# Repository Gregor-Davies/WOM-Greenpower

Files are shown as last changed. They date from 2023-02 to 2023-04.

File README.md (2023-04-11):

# Greenpower Winter Of Making

A telemetry system for a Greenpower racing go-kart (https://www.greenpower.co.uk/), built using LoRA and programmed with C++. This project has kindly been funded through the hack club winter of making grant program.

# Currently Implemented

- Temperature of the motor
- Speed of the vehicle
- Temperature of the batteries

TODO:

- Current sensor
- Braking notfications?
- Web app?
- SD Datalogging
- Bigger screens
- Graphing of results?
- Elapsed time of race
- Tyre pressure
- Strain sensor
- Better casing designs
- Gyroscope?
- Swith to imu?
- Battery voltage
- Test the range of the system
- Throttle position
- Battery Voltage
- Recording amp hours used
- Distance travelled
- Lap number

# System Diagram

Lora Diagram (1)

# Required Parts

| Product | Supplier/Link | Cost |
| --- | --- | --- |
| Heltec Lora32 v2  | https://bit.ly/3zlZaot Amazon  | $55  |
| DS18B20 Sensor| https://bit.ly/3VdB5J5  Amazon | $16 |
| 10000mah PowerBank | https://bit.ly/3v5uVju Amazon | $13 |
| 15k Ohm Resistors | https://bit.ly/3FLcQMF Amazon | $3 |
| 1k Potentiometer | https://bit.ly/3FJpsDI Amazon | $4 |
| 100nF Capacitors| https://bit.ly/3G6lmXE Amazon| $7 |
| Zener Diode | https://bit.ly/3HV55q9 Amazon | $2.5 |
| Perfboard | https://bit.ly/3G37gq5 Amazon | $6.5 |
| Right angle USB MICRO Cable | Already Have | $8 |
| Speed sensor | https://bit.ly/3WocDWD Amazon | $7 |
| 6.2k Resistors | https://bit.ly/3YDCV92 Amazon | $4.5 |
| Total | | $126.5 |

# Error Codes

- 1 LED BLINK: Oled initalization has failed, check if OLED pins are correct (By default they are) and if the OLED is visibly damaged.
- 2 LED BLINKS: No packet was recieved by the reciever, check antennas on both reciever and transmitter. 
- 3 LED BLINKS: Motor temperature is 85 C, this is normally an indicator that the DS18B20 sensors are broken or not working (Or your vehicle is running too hot).
- 4 LED BLINKS: Heatsink temperature is 85 C, this is normally an indicator that the DS18B20 sensors are broken or not working (Or your vehicle is running too hot).

## License

This project, code and all of it's respecting files is licensed under the AGPL v3 Copyleft license. This means that all projects utilising this code must also be opensource, please respect this.

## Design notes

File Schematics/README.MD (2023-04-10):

All the schematics for the project.

Battery schematic taken from https://forum.arduino.cc/t/the-cheapest-and-safest-method-to-read-car-battery-voltage/684897
Multiple ds18b20 sensors from https://randomnerdtutorials.com/esp32-multiple-ds18b20-temperature-sensors/

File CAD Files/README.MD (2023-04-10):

All the cad files for the project

Personally I printed the base station case on a ender 3 with the base standard quality Cura settings and at a 10% infill.

You will need to print 1 of everything apart for the battery holder where you will have to print 2.

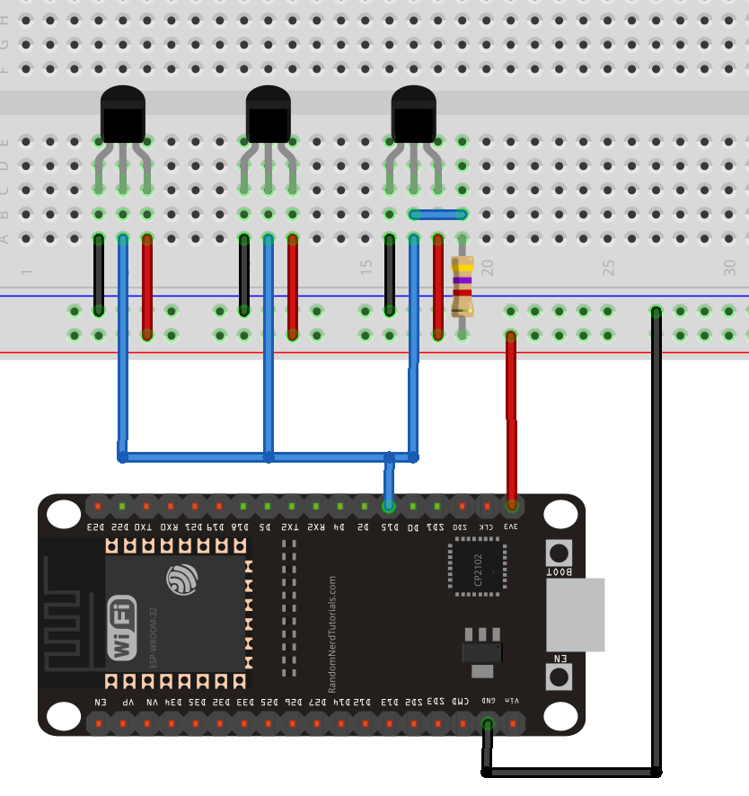
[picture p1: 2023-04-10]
Schematics/multiple_ds18b20_esp32_bb.png

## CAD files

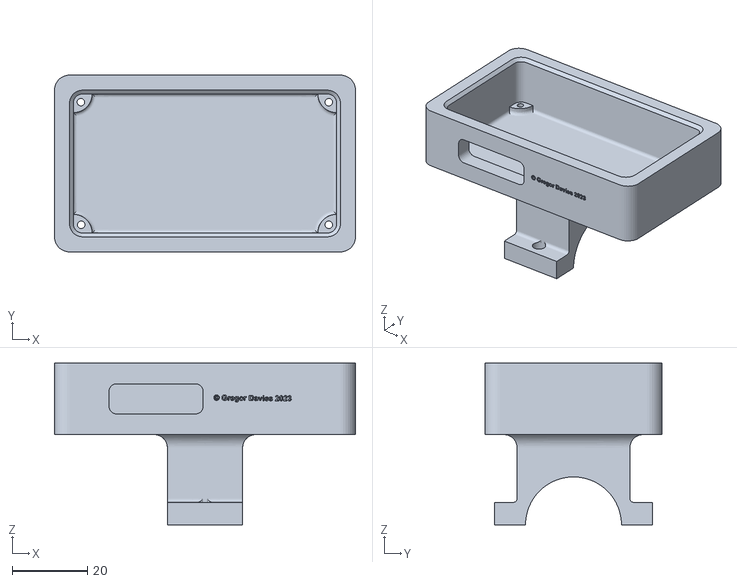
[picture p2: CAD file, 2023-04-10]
CAD Files/Greenpower temp case v7 Main.stl
80.0 x 47.0 x 43.0

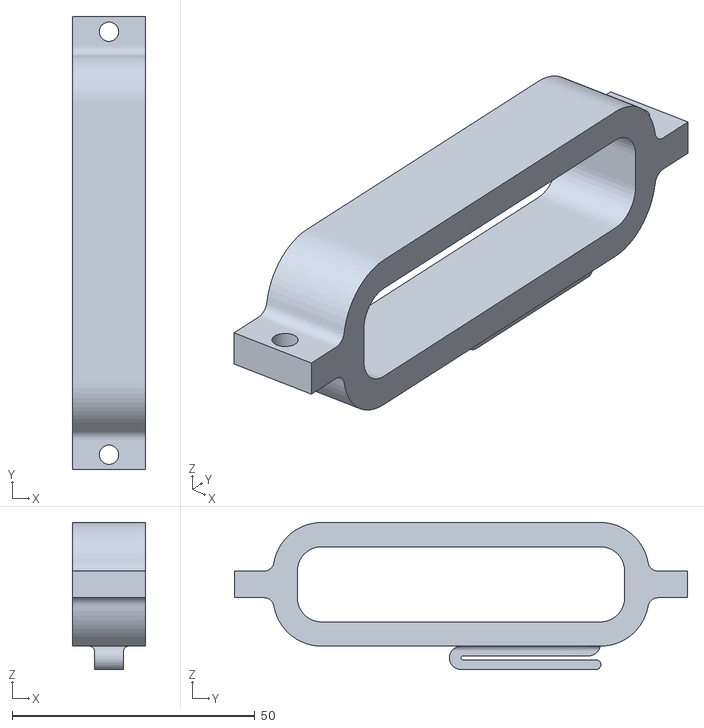
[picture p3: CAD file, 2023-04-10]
CAD Files/Battery Holder v1.stl
15.0 x 93.4 x 30.3

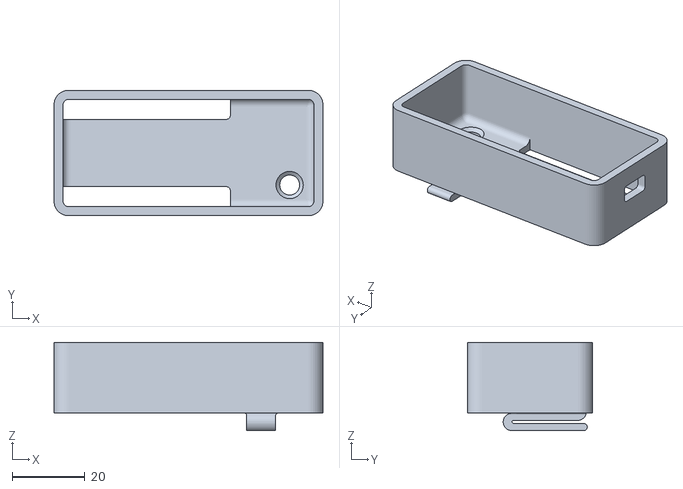
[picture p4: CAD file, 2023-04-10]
CAD Files/New heltec lora32 v2 case.stl
74.0 x 34.5 x 24.3

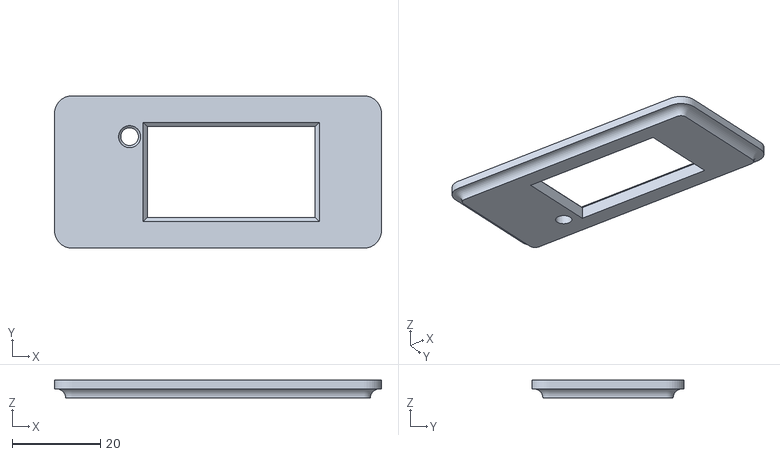
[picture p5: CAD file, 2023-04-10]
CAD Files/heltec lora32 v2 lid.stl
74.0 x 34.5 x 4.00

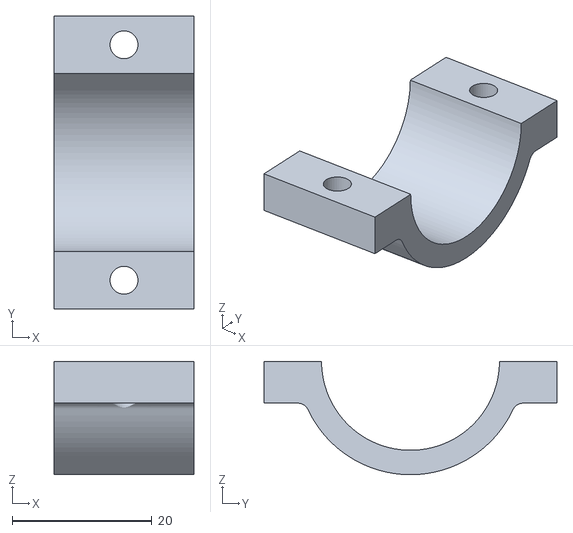
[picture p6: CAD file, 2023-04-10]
CAD Files/Greenpower temp case v7 loop.stl
20.0 x 42.0 x 16.2

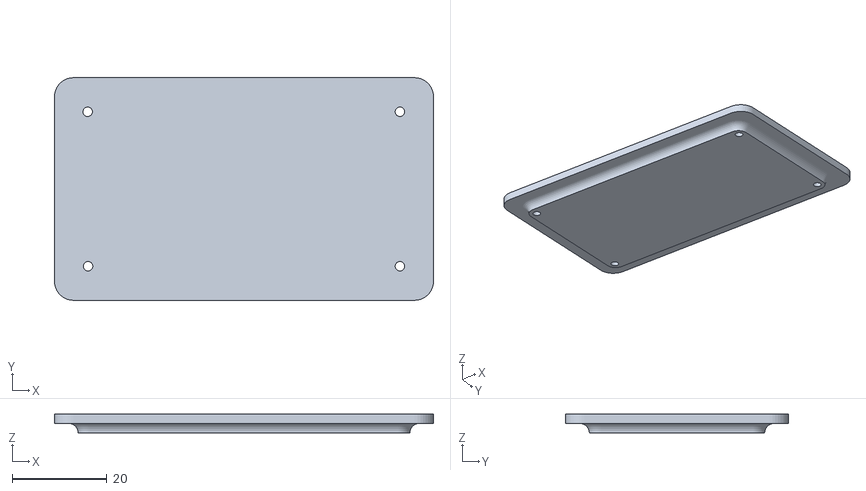
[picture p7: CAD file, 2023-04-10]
CAD Files/Greenpower temp case v7 lid.stl
80.0 x 47.0 x 4.00

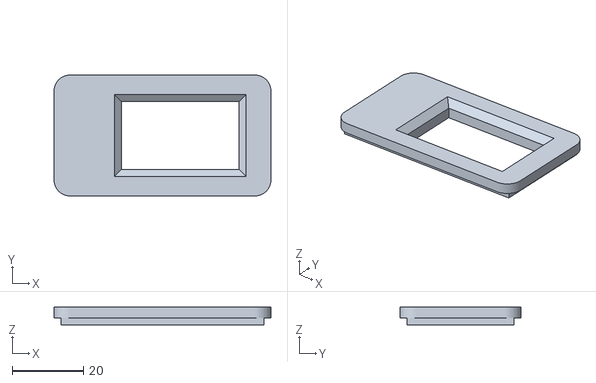
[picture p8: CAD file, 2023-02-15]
CAD Files/Case v2 Top.stl
61.0 x 34.0 x 5.00

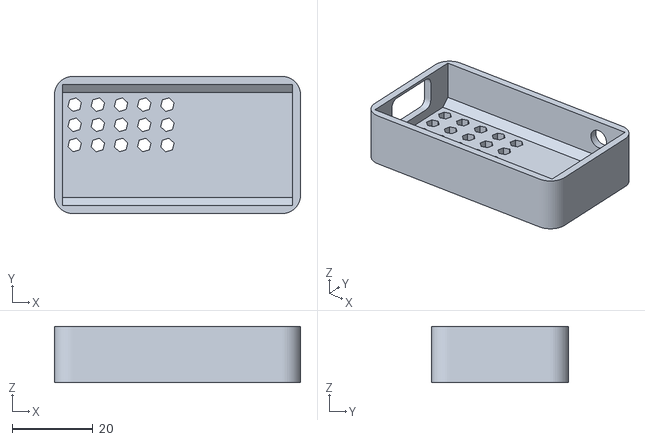
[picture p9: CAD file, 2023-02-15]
CAD Files/Case-Base v2.stl
61.0 x 34.0 x 14.0

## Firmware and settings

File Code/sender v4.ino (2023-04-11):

#include <LoRa.h>

// display stuff
#include <Wire.h>
#include <Adafruit_GFX.h>
#include <Adafruit_SSD1306.h>

// this stuff is for the temp sensor
#include <OneWire.h>
#include <DallasTemperature.h>

// defining the lora pins
#define ss 18
#define rst 14
#define dio0 26

// setting up the onewirebus on pin 23
const int oneWireBus = 23;

// setting up a one wire instance
OneWire oneWire(oneWireBus);

//pass one wire under the dallas temp lib
DallasTemperature sensors(&oneWire);

// Addressing the 2 temp sensors
DeviceAddress temp1 = {0x28, 0x35, 0xF7, 0x2E, 0xA1, 0x21, 0x1, 0x8C };
DeviceAddress temp2 = {0x28, 0xC9, 0x3, 0x33, 0xA1, 0x21, 0x1, 0x9f };

// defining the oled used
#define OLED_SDA 4
#define OLED_SCL 15 
#define OLED_RST 16
#define SCREEN_WIDTH 128 // OLED display width, in pixels
#define SCREEN_HEIGHT 64 // OLED display height, in pixels

// speed sensor is on pin check out the heltec lora32 v2 pin out diagram
const int LM393 = 17;
int counter = 0;

// starting the oled
Adafruit_SSD1306 display(SCREEN_WIDTH, SCREEN_HEIGHT, &Wire, OLED_RST);

void setup() {
  attachInterrupt(digitalPinToInterrupt(LM393), count, RISING);
  Serial.begin(115200);
  //reset OLED display via software
  pinMode(OLED_RST, OUTPUT);
  digitalWrite(OLED_RST, LOW);
  delay(20);
  digitalWrite(OLED_RST, HIGH);
  //initialize OLED
  Wire.begin(OLED_SDA, OLED_SCL);
  if(!display.begin(SSD1306_SWITCHCAPVCC, 0x3c, false, false)) { // Address 0x3C for 128x32
    Serial.println(F("SSD1306 allocation failed"));
    digitalWrite(LED_BUILTIN, HIGH); // error code 1: see github
    digitalWrite(LED_BUILTIN, LOW);    
    for(;;); // Don't proceed, loop forever
  }
  // setting the lora pins
  LoRa.setPins(ss, rst, dio0);
  LoRa.begin(866E6);
  LoRa.setSyncWord(0xF3);
  sensors.begin();
}

void count() {
  counter++;
}

// gets the sensors
void Sensors() {
  // Allowing the sensors time to do their stuff
  delay(500);
  char nonFloTemp[4];
  char nonFloBatteryTemp[4];
  char speedBuffer[15];
  char mTemp[25];
  char bTemp[25];
  char packetToSend[55];
  display.clearDisplay();
  // setting the colour to white and font size - this should always be white no matter what oled colour
  display.setTextColor(WHITE);
  display.setTextSize(1);
  // this converts the number to rpm and into kmh, the 60 is for rpm and the first number is wheel diameter in cm k = d * r * 0.001885
  int speed = 2.57 * counter * 60 * 0.001885;
  // getting the temp from the temperature sensors
  sensors.requestTemperatures();
  // getting the temp sensor at index 0 and converts the float to a string for sprintf
  float mTemperature = sensors.getTempC(temp1);
  dtostrf(mTemperature, 2, 0, nonFloTemp);
  if(mTemperature = 85) {
    digitalWrite(LED_BUILTIN, HIGH); // error code 3: see github
    digitalWrite(LED_BUILTIN, LOW);    
    digitalWrite(LED_BUILTIN, HIGH); //and yes I am doing like this as otherwise I would have to store an additional counter variable which is more memory intensive than just spaghetti code like this.
    digitalWrite(LED_BUILTIN, LOW);
    digitalWrite(LED_BUILTIN, HIGH); 
    digitalWrite(LED_BUILTIN, LOW);
  }
   // same thing but at index 1
  float bTemperature = sensors.getTempC(temp2);
  dtostrf(bTemperature, 2, 0, nonFloBatteryTemp);
  if(bTemperature = 85) {
    digitalWrite(LED_BUILTIN, HIGH); // error code 4: see github
    digitalWrite(LED_BUILTIN, LOW);    
    digitalWrite(LED_BUILTIN, HIGH); 
    digitalWrite(LED_BUILTIN, LOW);
    digitalWrite(LED_BUILTIN, HIGH); 
    digitalWrite(LED_BUILTIN, LOW);
    digitalWrite(LED_BUILTIN, HIGH); 
    digitalWrite(LED_BUILTIN, LOW);
  }
  // combines the speed and motor
  sprintf(speedBuffer, "SPEED: %d km/h", speed);
  sprintf(mTemp, "MOTOR TEMP: %sC", nonFloTemp);
  sprintf(bTemp, "BATTERY TEMP: %sC", nonFloBatteryTemp);
  // prints the speed, then sets the cursor one down and prints the temperature
  // sets cursor at 0
  display.setCursor(0,0);
  display.print(speedBuffer);
  display.setCursor(0,10);  
  display.print(mTemp);
  display.setCursor(0,20);
  display.print(bTemp);
  // Combining the things to send as one packet
  snprintf(packetToSend, 55, "%s,%s,%s", speedBuffer, mTemp, bTemp);
  // begins the lora packet
  LoRa.beginPacket();
  LoRa.print(packetToSend);
  LoRa.endPacket();
  counter = 0;
}

void loop() {
  Sensors();
  display.display();
}

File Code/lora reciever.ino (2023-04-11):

// lora libraries
#include <LoRa.h>

// lora pins
#define ss 18
#define rst 14
#define dio0 26

// display stuff
#include <Wire.h>
#include <Adafruit_GFX.h>
#include <Adafruit_SSD1306.h>

// defining the oled used
#define OLED_SDA 4
#define OLED_SCL 15 
#define OLED_RST 16
#define SCREEN_WIDTH 128 // OLED display width, in pixels
#define SCREEN_HEIGHT 64 // OLED display height, in pixels

// starting the oled
Adafruit_SSD1306 display(SCREEN_WIDTH, SCREEN_HEIGHT, &Wire, OLED_RST);

void setup() {
  LoRa.setPins(ss, rst, dio0);
  Serial.begin(115200);
  pinMode(LED_BUILTIN, OUTPUT); // led for failures
  LoRa.begin(866E6);
  LoRa.setSyncWord(0xF3);
  digitalWrite(LED_BUILTIN, HIGH);
  //reset OLED display via software
  pinMode(OLED_RST, OUTPUT);
  digitalWrite(OLED_RST, LOW);
  delay(20);
  digitalWrite(OLED_RST, HIGH);
  //initialize OLED
  Wire.begin(OLED_SDA, OLED_SCL);
  if(!display.begin(SSD1306_SWITCHCAPVCC, 0x3c, false, false)) { // Address 0x3C for 128x32
    Serial.println(F("SSD1306 allocation failed"));
    digitalWrite(LED_BUILTIN, HIGH); // error code 1: see github
    digitalWrite(LED_BUILTIN, LOW);    
    for(;;); // Don't proceed, loop forever
  }
}

void getLora() {
  delay(50);
  int packetSize = LoRa.parsePacket();
  if (packetSize) {
    while (LoRa.available()) {
      // read the string from lora
    String receivedString = LoRa.readString();

    char charArray[receivedString.length() + 1]; // creates a char array the length of the packet length but +1
    receivedString.toCharArray(charArray, receivedString.length() + 1); // creates the char array

    // split the charArray
    char* ptr = strtok(charArray, ","); // parses the char array by the "," delimiter which is set on the transmitter side
    String speed(ptr);
    ptr = strtok(NULL, ",");
    String mTemp(ptr);
    ptr = strtok(NULL, ",");
    String bTemp(ptr);

    display.clearDisplay();
    display.setTextColor(WHITE); // this should always be white
    display.setTextSize(1);

    // Displays the split strings
    display.setCursor(0,0);
    display.print(speed);
    display.setCursor(0, 10);
    display.print(mTemp);
    display.setCursor(0,20);
    display.print(bTemp);
    display.setCursor(0, 30);
    display.print("RSSI: ");
    display.print(LoRa.packetRssi());
    }
  } else {
      digitalWrite(LED_BUILTIN, HIGH); // error code 2: see github
      digitalWrite(LED_BUILTIN, LOW);
      digitalWrite(LED_BUILTIN, HIGH);
      digitalWrite(LED_BUILTIN, LOW);   
  }
}

void loop() {
  getLora();
  display.display();
}

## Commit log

2023-03-30 Newest version of the telem with motor temp added
2023-03-31 Updated sender code with additional temp sensor
2023-04-10 Added in vehicle case
    [Greenpower heltec lora 32 v2 case body.stl, Greenpower heltec lora 32 v2 case v5 lid.stl]
2023-04-10 Case for the temp board
    [Greenpower temp case v7 Main.stl, Greenpower temp case v7 lid.stl, Greenpower temp case v7 loop.stl]
